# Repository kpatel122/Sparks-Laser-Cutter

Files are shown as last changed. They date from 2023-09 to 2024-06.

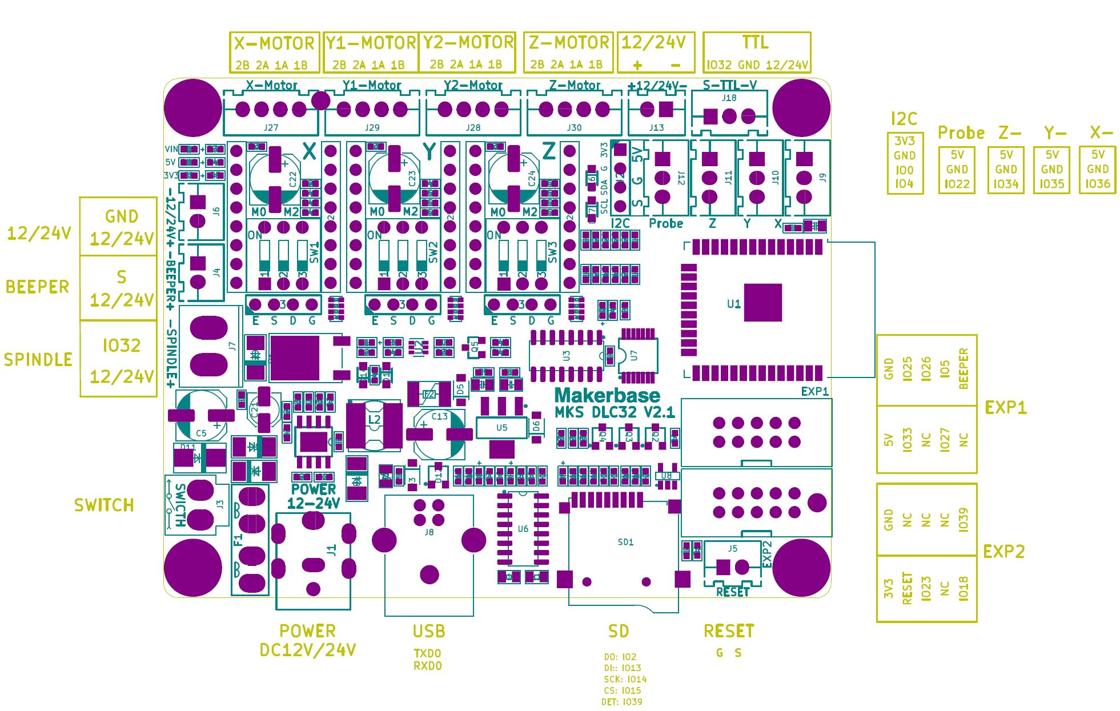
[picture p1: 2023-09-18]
DLC32/mks_dlc32_v21_003.jpg

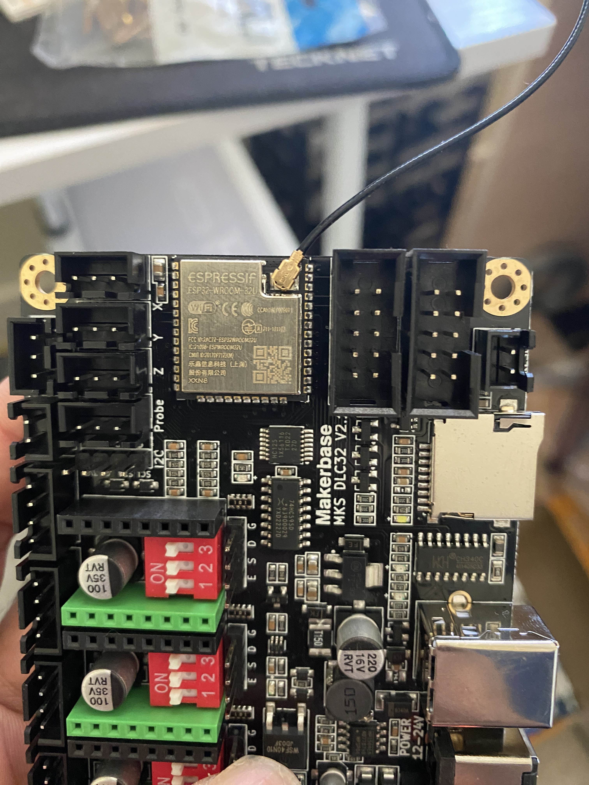
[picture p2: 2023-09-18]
DLC32/IMG_1829.JPG

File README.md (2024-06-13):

# Sparks-Laser-Cutter
CO2 Laser cutter

(https://www.youtube.com/watch?v=hKLUTKVeXzE)

Shield: [][cc-by-nc-sa]

This work is licensed under a
[Creative Commons Attribution-NonCommercial-ShareAlike 4.0 International License][cc-by-nc-sa].

[][cc-by-nc-sa]

[cc-by-nc-sa]: http://creativecommons.org/licenses/by-nc-sa/4.0/
[cc-by-nc-sa-image]: https://licensebuttons.net/l/by-nc-sa/4.0/88x31.png
[cc-by-nc-sa-shield]: https://img.shields.io/badge/License-CC%20BY--NC--SA%204.0-lightgrey.svg

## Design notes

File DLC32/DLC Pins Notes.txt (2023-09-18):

MKS        PSU
S    ->    TTL   (~0-5 PWM signal)

TTL  ->    GND   (Common GND)

GPIO_NUM_25 ->  TH (trigger high)

#define LASER_OUTPUT_PIN           GPIO_NUM_32
#define LASER_ENABLE_PIN           GPIO_NUM_25

GPIO_NUM_26 FEED_HOLD
GPIO_NUM_33 CYCLE_START
GPIO_NUM_27 RESET

GPIO_NUM_18 or 23  DOOR

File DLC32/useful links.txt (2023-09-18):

 
https://github.com/bdring/Grbl_Esp32/wiki/Setting-Up-Spindles-and-Lasers

https://github.com/bdring/Grbl_Esp32/wiki/Spindle-Types

http://wiki.fluidnc.com/en/hardware/3rd-party/MKS_DLC32

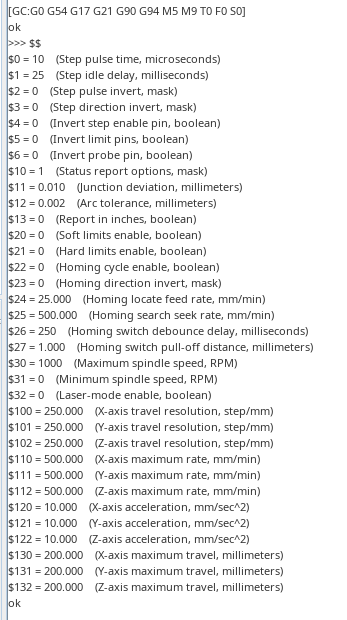
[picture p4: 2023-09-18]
DLC32/GRBL_Arduino_Stock.png

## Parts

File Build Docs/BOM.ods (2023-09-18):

Piece | Type | Size | Quantity | 1m Pieces needed | Total | Left Over | Left Quantity | 9 | 1000
Base Frame Front | 2040 | 712 | 2 | 2 |  | 288 | 2 | 3 | 1000
Base Frame Side | 2040 | 635 | 2 | 2 |  | 365 | 2 |  | 640 | E1
Base Frame Height Front | 2040 | 220 | 2 |  |  |  |  | 2 | 400 | E2
Base Frame Height Back | 2040 | 264 | 2 |  |  |  |  |  | 365 | E3
 |  |  |  |  |  |  |  | 2 | 340 | E4
Gantry Frame Front | 2040 | 752 | 2 | 2 |  | 248 | 2
Gantry Frame Side | 2040 | 635 | 2 | 2 |  | 365 | 2
Gantry X Axis | 2040 | 845 | 1 | 1 |  | 155 | 1
 |  |  |  |  | 9
Outer Frame Front | 2020 | 882 | 5 | 5 |  | 118 | 5
Outer Frame Side | 2020 | 800 | 4 | 4 |  | 200 | 4
Outer Frame Height | 2020 | 392 | 4 | 2 |  | 216 | 2
Lid Front | 2020 | 877 | 3 | 3 |  | 123 | 3
Lid Side | 2020 | 595 | 2 | 2 |  | 405 | 2
Lid Height | 2020 | 100 | 2 | 0 | Outer Frame Front
Bed Front | 2020 | 670 | 2 | 2 |  | 330
Bed Side | 2020 | 450 | 2 | 1 |  | 100
Electrics Enclosure Front | 2020 | 200 | 4 | 0 | Outer Frame Side
Electrics Enclosure Side | 2020 | 615 | 2 | 1 | “+E1” | 385 | 1
Electrics Enclosure Height | 2020 | 392 | 3 | 1 | “+E2” | 216
Laser Encosure Front | 2020 | 240 | 2
Laser Encosure Back | 2020 | 440 | 2
Laser Encosure Side | 2020 | 125 | 2
Laser Encosure Height | 2020 | 150 | 2
 |  |  |  | 21
 |  |  |  | 1000 | 800
 |  |  | 1 | 8 | 8 | 2

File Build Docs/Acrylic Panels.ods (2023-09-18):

Part | Size(CM) | Colour | Thickness | V | Trent | 96.02(Inc Del)
Lid Front | 92.5x26 | red transparent | 3mm | V | R
Lid Top | 92.5x61.5 | red transparent | 3mm | V | R
Shell Front | 94.5x17.8 | clear | 3mm | V | R
Shell Side | 82x44 | clear | 3mm | V | R
Electronics Front | 45x20 | clear | 3mm | V | R
Electronics Side | 61x45 | clear | 3mm | V | R
Tube Top 1 | 95x20.5 | clear | 3mm | V | R
Tube Top 2 | 20x18 | clear | 3mm | V | R
Tube Top 3/Bottom | 20x25(QUANT 2) | clear | 3mm | V | R
Tube Side | 28.5x20 |  |  | V | R
Tube Front | 28.5x25 |  |  | V | R
Tube Back | 28.5x17 |  |  | V | R

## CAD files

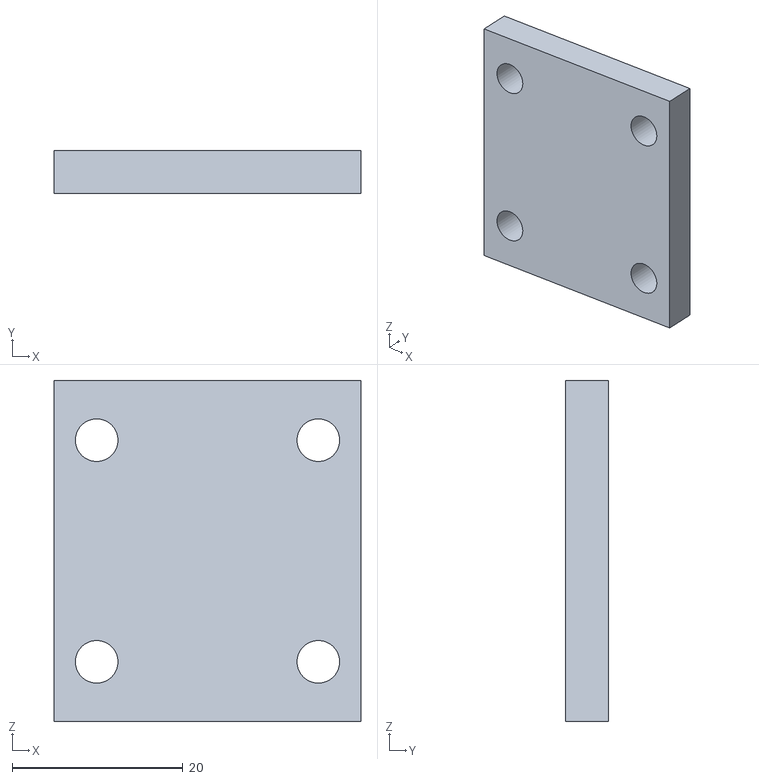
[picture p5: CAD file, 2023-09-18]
3D Printed/Shim_5.stl
36.0 x 5.00 x 40.0

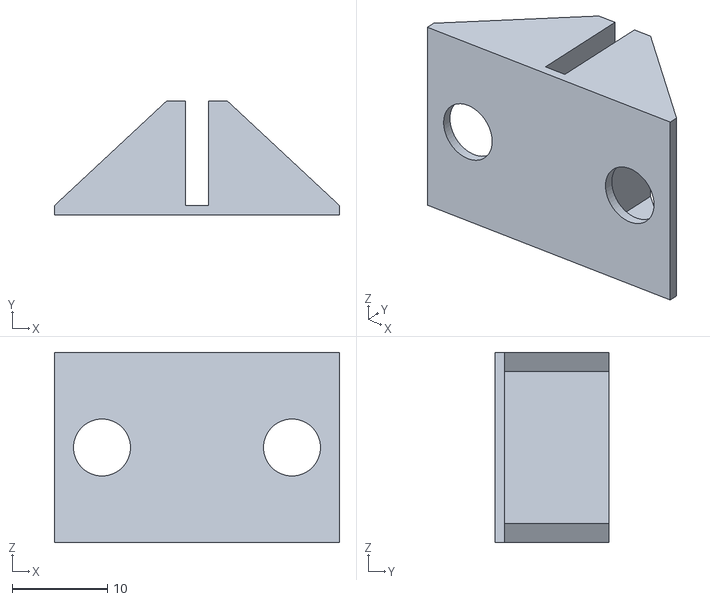
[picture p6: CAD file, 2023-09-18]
3D Printed/Bed_Rail_Holder_2.stl
30.0 x 12.0 x 20.0

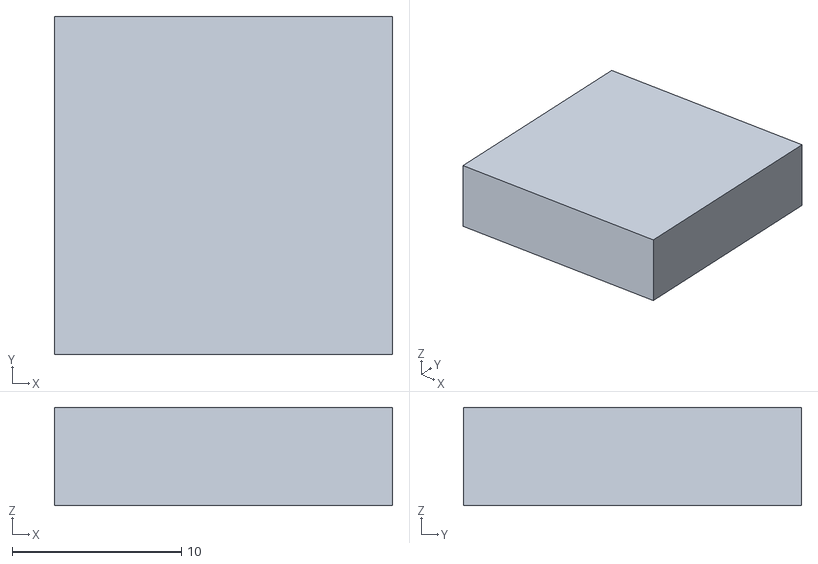
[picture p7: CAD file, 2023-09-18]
3D Printed/Focus_Jig_5-8.stl
20.0 x 20.0 x 5.80

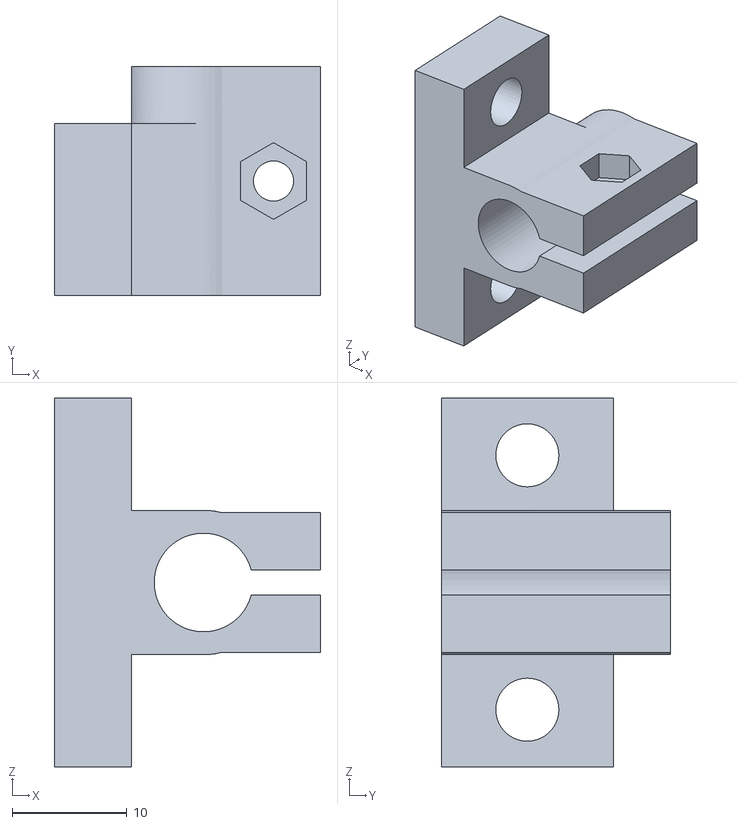
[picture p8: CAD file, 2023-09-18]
3D Printed/Leadscrew_Clamp_V4.stl
23.2 x 20.0 x 32.2

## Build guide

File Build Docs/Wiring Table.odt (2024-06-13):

GRBL ESP32 | DLC32 Pin | Connection
LASER_OUTPUT_PIN | GPIO_NUM_32 (‘S’ on board) | PS IN
LASER_ENABLE_PIN (Active High) | GPIO_NUM_25 | PS H
CONTROL_FEED_HOLD_PIN | GPIO_NUM_33 | Feed Hold Switch (Amber)
CONTROL_CYCLE_START_PIN | GPIO_NUM_4 | Feed Resume Switch (Green)
N/A (Hard Reset) | Reset | Reset Switch (Red)
N/A (Ground) | TTL | GND

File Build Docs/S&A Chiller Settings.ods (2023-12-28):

Code | Desc | Value | Applicable Constant Mode | Notes | Hold “SET” and “UP arrow” together, enter password set values with “SET” Key, Save changes with RST Key
F0 | Temperature Setting | 21.5 |  | 21.5(F0)+3(F2)= 24.5 Target temp
F1 | Temperature difference values | x | NO
F2 | Cooling Hysteresis | 3
F3 | Way of Control | 0
F4 | Alarm for over high water Temp | 4.5 |  | 21 (F0) + 4.5 (F4)= 25.5= Alarm E2
F5 | Alarm for over low water Temp | 7.5 |  | 21 (F0) – 7.5 (F5)= 13.5 = Alarm
F6 | Alarm for over high room temp | 40
F7 | Password | 8
F8 | The highest allowed water temp | 25.5
F9 | The lowest allowed water temp | 13.5

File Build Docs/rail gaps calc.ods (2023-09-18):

width | num rails | gap
615 | 6 | 87.8571428571429

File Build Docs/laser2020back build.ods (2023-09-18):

Length | Quantity
38 | 1 | D
40 | 2 | D
20 | 2 | D
24.5 | 2 | D
42.5 | 1
25 | 2

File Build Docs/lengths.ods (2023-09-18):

length | quantity
400 | 5 | 2020
820 | 4 | 2020 | 820
655 | 2 | 2020
920 | 5 | 2020 | Do 2 for a check

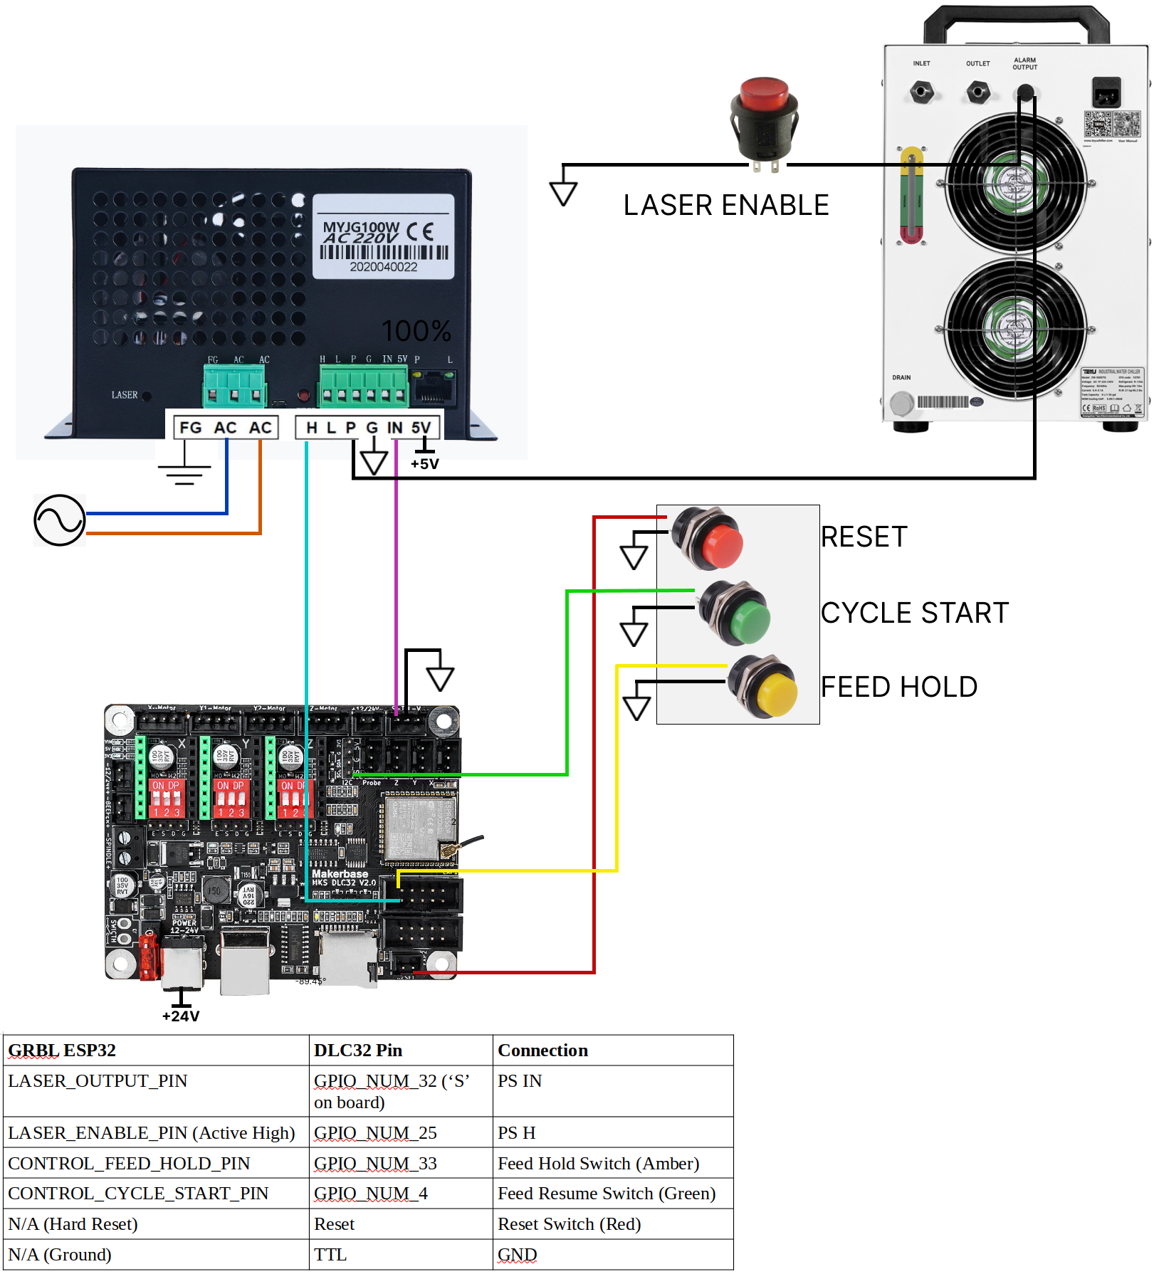
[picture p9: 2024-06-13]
Build Docs/laser wiring.jpg

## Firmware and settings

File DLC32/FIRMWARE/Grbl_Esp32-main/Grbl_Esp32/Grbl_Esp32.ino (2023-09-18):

/*
  Grbl_ESP32.ino - Header for system level commands and real-time processes
  Part of Grbl
  Copyright (c) 2014-2016 Sungeun K. Jeon for Gnea Research LLC

	2018 -	Bart Dring This file was modified for use on the ESP32
					CPU. Do not use this with Grbl for atMega328P

  Grbl is free software: you can redistribute it and/or modify
  it under the terms of the GNU General Public License as published by
  the Free Software Foundation, either version 3 of the License, or
  (at your option) any later version.
  Grbl is distributed in the hope that it will be useful,
  but WITHOUT ANY WARRANTY; without even the implied warranty of
  MERCHANTABILITY or FITNESS FOR A PARTICULAR PURPOSE.  See the
  GNU General Public License for more details.
  You should have received a copy of the GNU General Public License
  along with Grbl.  If not, see <http://www.gnu.org/licenses/>.
*/

//original ESP32 BDRING

#include "src/Grbl.h"


void setup() {
    grbl_init();
}

void loop() {
    run_once();
}

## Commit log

2023-09-25 cleaned up config settings
    [settings_before_flash_grbl.txt]
2023-12-28 removed unused machine definitions, modified build instructions
    [alarm_codes_en_US.csv, build_option_codes_en_US.csv, error_codes_en_US.csv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]
2023-12-28 added chiller settings, cleaned up docs
    [Acrylic Panels.ods, BOM.ods, KP-Modified-Grbl-Esp32.txt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]
2023-12-30 fixed Z steps per mm
    0.5->0.6
    Changed default values max rates, acceleration & homing speeds to match lightburn's verified settings
    Changed Z steps per mm to correct value from 80 to 400
2024-06-13 Added CAD Model
    Cleaned up repo
    [S&A Chiller Settings.ods, tmc2209_calc.ods]

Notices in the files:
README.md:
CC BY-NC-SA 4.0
